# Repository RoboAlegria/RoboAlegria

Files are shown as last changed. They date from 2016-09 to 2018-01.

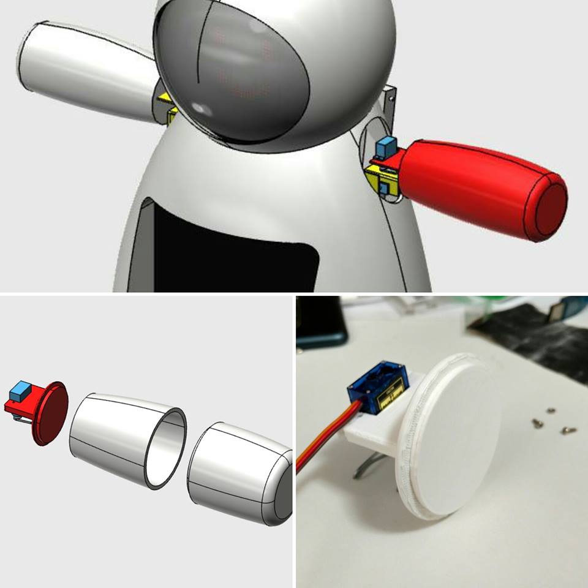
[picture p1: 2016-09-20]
modelo 3D/carenagem/images/impressão 3D-2.jpg

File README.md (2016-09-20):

# Robo da Alegria
Projeto de código aberto, com o objetivo de compartilhar conhecimentos sobre eletrônica, robótica e programação de computadores.

O objetivo geral do projeto é criar um Robô para ser utilizado no trabalho de ONGs como o Doutores da Alegria.

A estrutra dos diretórios está organizada para

appInventor: código do AppInventor para testar a comunicação via bluetooth com o Robô.
arduino: código do Arduino para o controle da expressão facial (matriz de leds)
images: imagens utilizadas no projeto
webservice: código da parte web para a interface que o operador controlar o robô
Mais informações na wiki do projeto: https://github.com/RoboAlegria/RoboAlegria/wiki

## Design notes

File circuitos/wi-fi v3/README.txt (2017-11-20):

Especificação:
- Acionamento de até 6 servo motores (J1, J2, J3, J4, J5 e J6)
- Acionamento de array de matrizes de LED
- Comunicação através de wi-fi (ESP8266)
- Alimentação dos servo motores por bateria externa

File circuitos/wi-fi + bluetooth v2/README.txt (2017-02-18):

Especificação do Shield:
- Shield para Arduino Uno
- Acionamento de até 5 servo motores (J1, J2, J3, J4 e J5)
- Acionamento de array de matrizes de LED (J6)
- Comuinicação através de bluetooth (HC-05 ou HC-06) (J7)
- Comunicação através de wi-fi (ESP8266) (J8)
- Alimentação do Arduino através de bateria externa (J15) - Colocar jumper em J12 para alimentação externa. Sem o jumper a alimentação será através da porta USB
- Alimentação dos servo motores por bateria externa (colocando jumper em J13 na posição +6V) ou diretamente do regulador de 5V do Arduino (colocando jumper em J13 na posição +5V)
- Acionamento de até quatro motores DC (J9 e J10)
- Remover jumper do conector J11 para programação
- Barramento para alimentação externa +5V de outros periféricos (J16 e J17)
- Pinos para entradas/saídas analógicas/digitais adicionais (J18)

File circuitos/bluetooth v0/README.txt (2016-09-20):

Especificação do Shield:
- Shield para Arduino Uno
- Acionamento de até 2 servo motores
- Acionamento de array de matrizes de LED
- Comuinicação através de bluetooth (HC-05 ou HC-06)

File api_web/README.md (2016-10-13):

# Robô da Alegria  

## API para desenvolvimento, simulando as ações do robô.  
  
O objeto deste API é simular as ações do robô para os desenvolvedores de aplicativos usarem os mesmo comandos que serão recebidos pelo robô.  

### Descrição:  
A URL inicial (/) mostra em uma página html a lista de comandos válidos;  
A URL /command-list mostra em formato JSON a lista de comandos válidos;  
A URL /?{PARAMETRO}={COMANDO} mostra o comando enviado;  

API dispinivel online pelo endereço: http://robodaalegria.hmxweb.com/

API desenvolvida com PHP, utilzando o microframework Slim.

http://www.slimframework.com

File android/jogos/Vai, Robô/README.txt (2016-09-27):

Por: Igor Fonseca Albuquerque
Baseado no jogo Droid-Run-Jump por Donald E. Llopis 2011 (https://github.com/machinezilla/DroidRunJump)

Um jogo de corrida para Android.

Desenolvido usando o Android 21.0 SDK.

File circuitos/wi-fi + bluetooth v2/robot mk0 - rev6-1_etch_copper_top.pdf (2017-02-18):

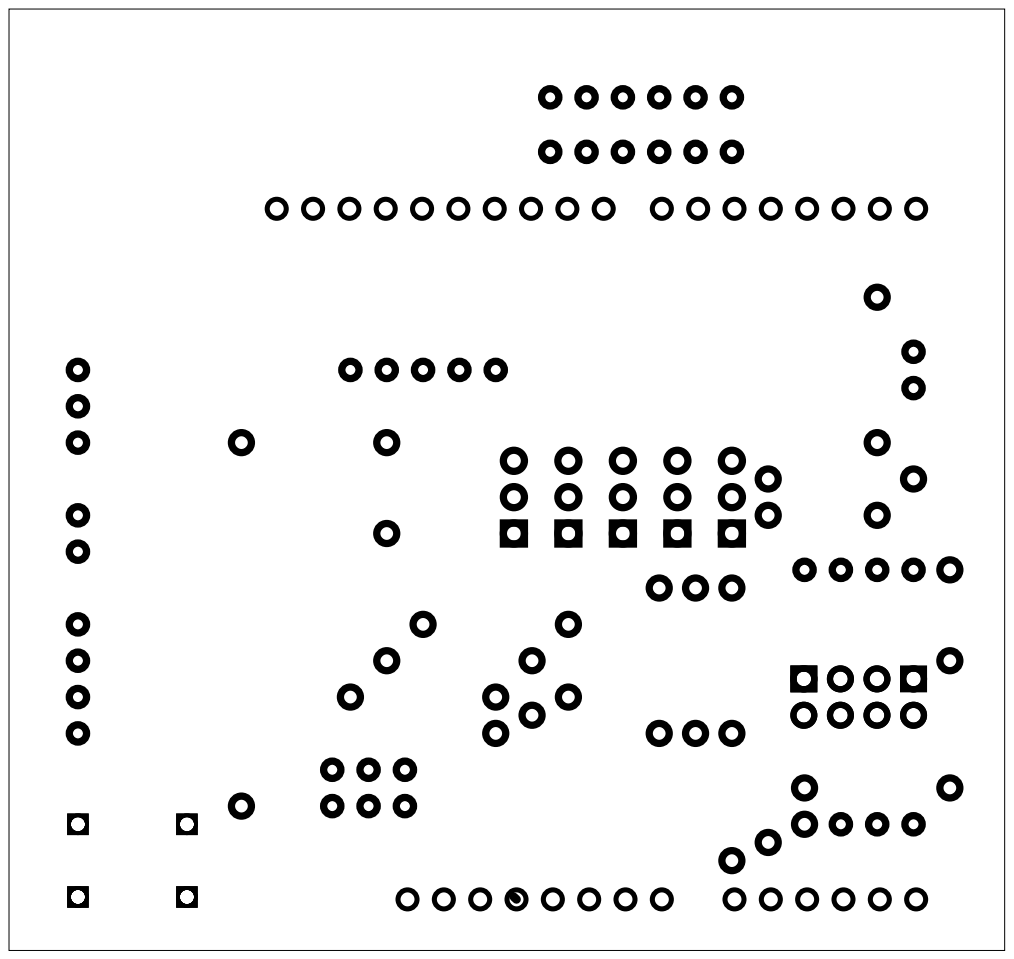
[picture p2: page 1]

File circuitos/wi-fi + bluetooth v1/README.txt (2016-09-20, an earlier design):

Especificação do Shield:
- Shield para Arduino Uno
- Acionamento de até 4 servo motores (J2, J3, J9 e J10)
- Acionamento de array de matrizes de LED (J8)
- Comuinicação através de bluetooth (HC-05 ou HC-06) (J7)
- Comunicação através de wi-fi (ESP8266) (U3)
- Alimentação dos servo motores por bateria externa (via USB em U2) ou diretamente do regulador de 5V do Arduino (seleção pelo jumper J13)

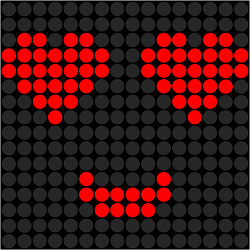
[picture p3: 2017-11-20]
interface html/full/images/rosto11.png

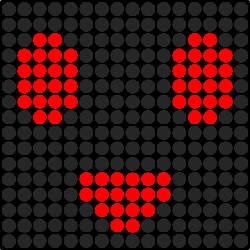
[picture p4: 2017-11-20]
interface html/full/images/rosto2.png

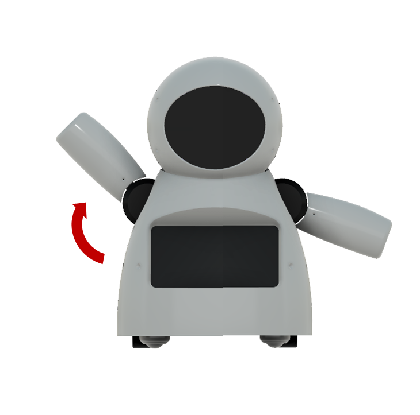
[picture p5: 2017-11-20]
interface html/full/images/mov02.png

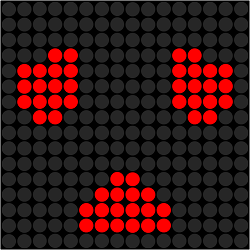
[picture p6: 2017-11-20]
interface html/full/images/rosto4.png

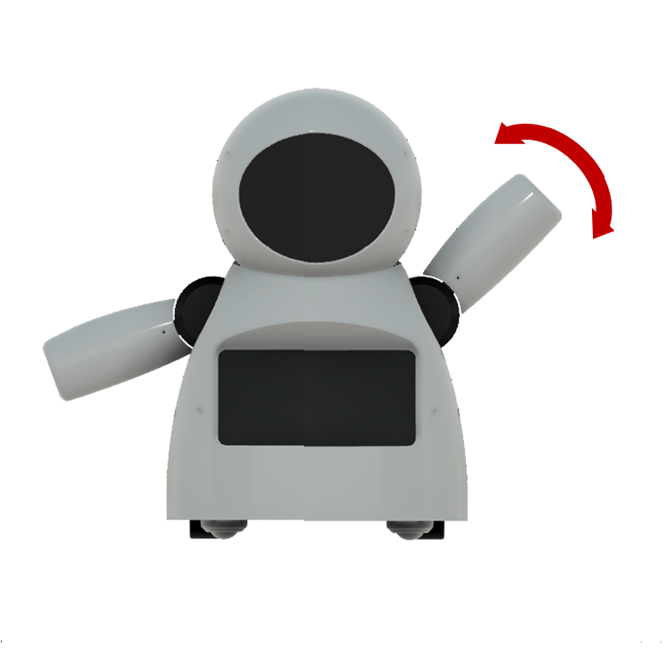
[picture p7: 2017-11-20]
interface html/full/images/mov09.png

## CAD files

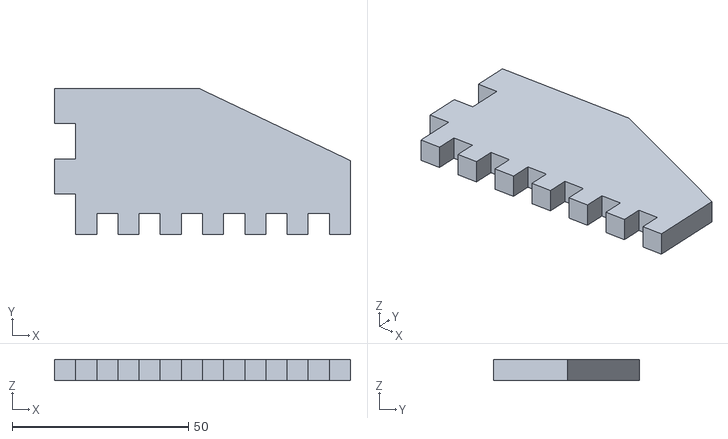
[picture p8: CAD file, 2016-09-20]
modelo 2D/p9.stl
84.0 x 41.5 x 6.00

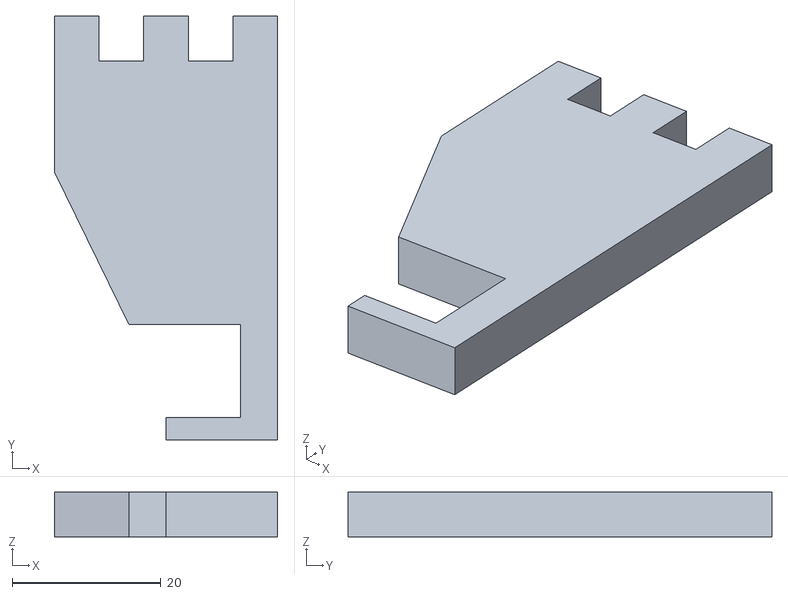
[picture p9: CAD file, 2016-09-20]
modelo 2D/p8.stl
30.0 x 57.0 x 6.00

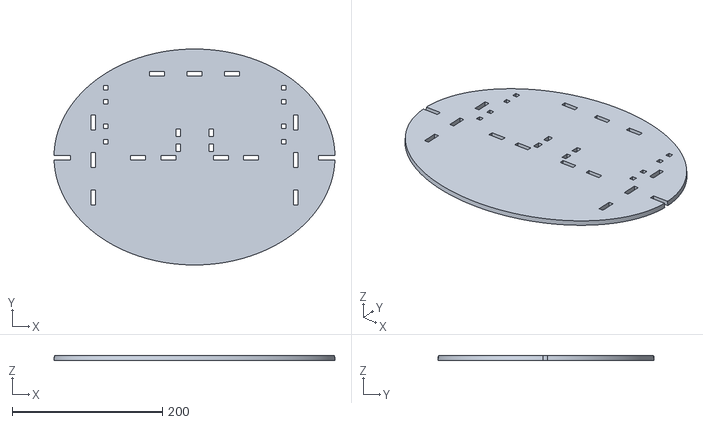
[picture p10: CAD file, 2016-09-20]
modelo 2D/p2.stl
374.3 x 287.6 x 6.00

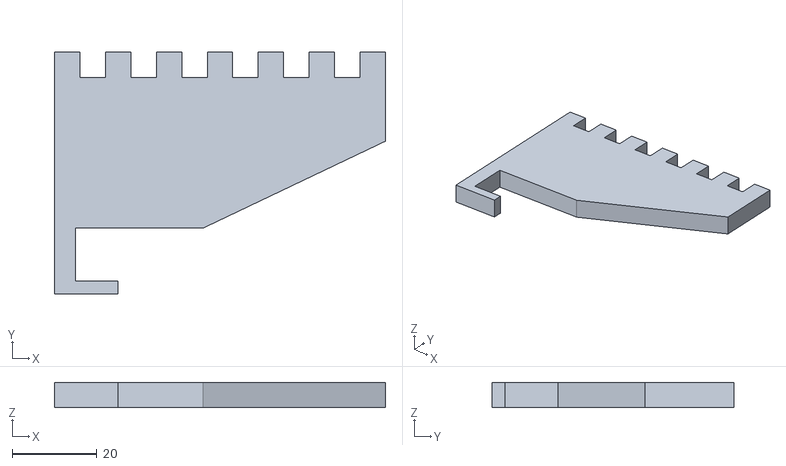
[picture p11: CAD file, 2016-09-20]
modelo 2D/p7.stl
78.0 x 57.0 x 6.00

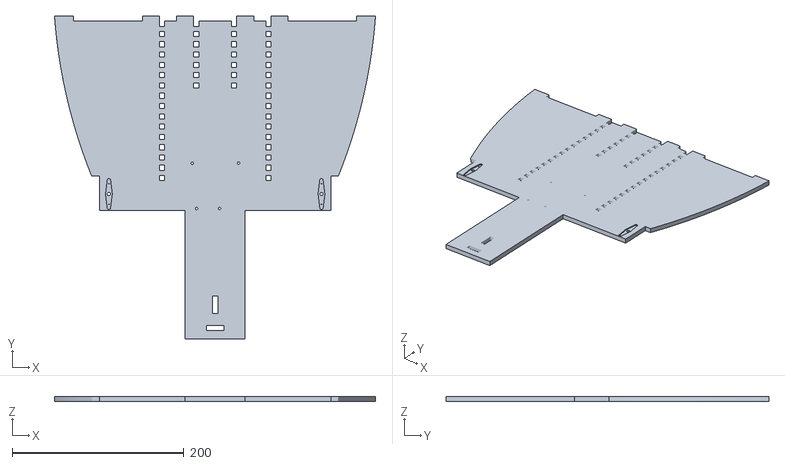
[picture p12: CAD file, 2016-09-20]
modelo 2D/p6.stl
374.3 x 376.6 x 6.00

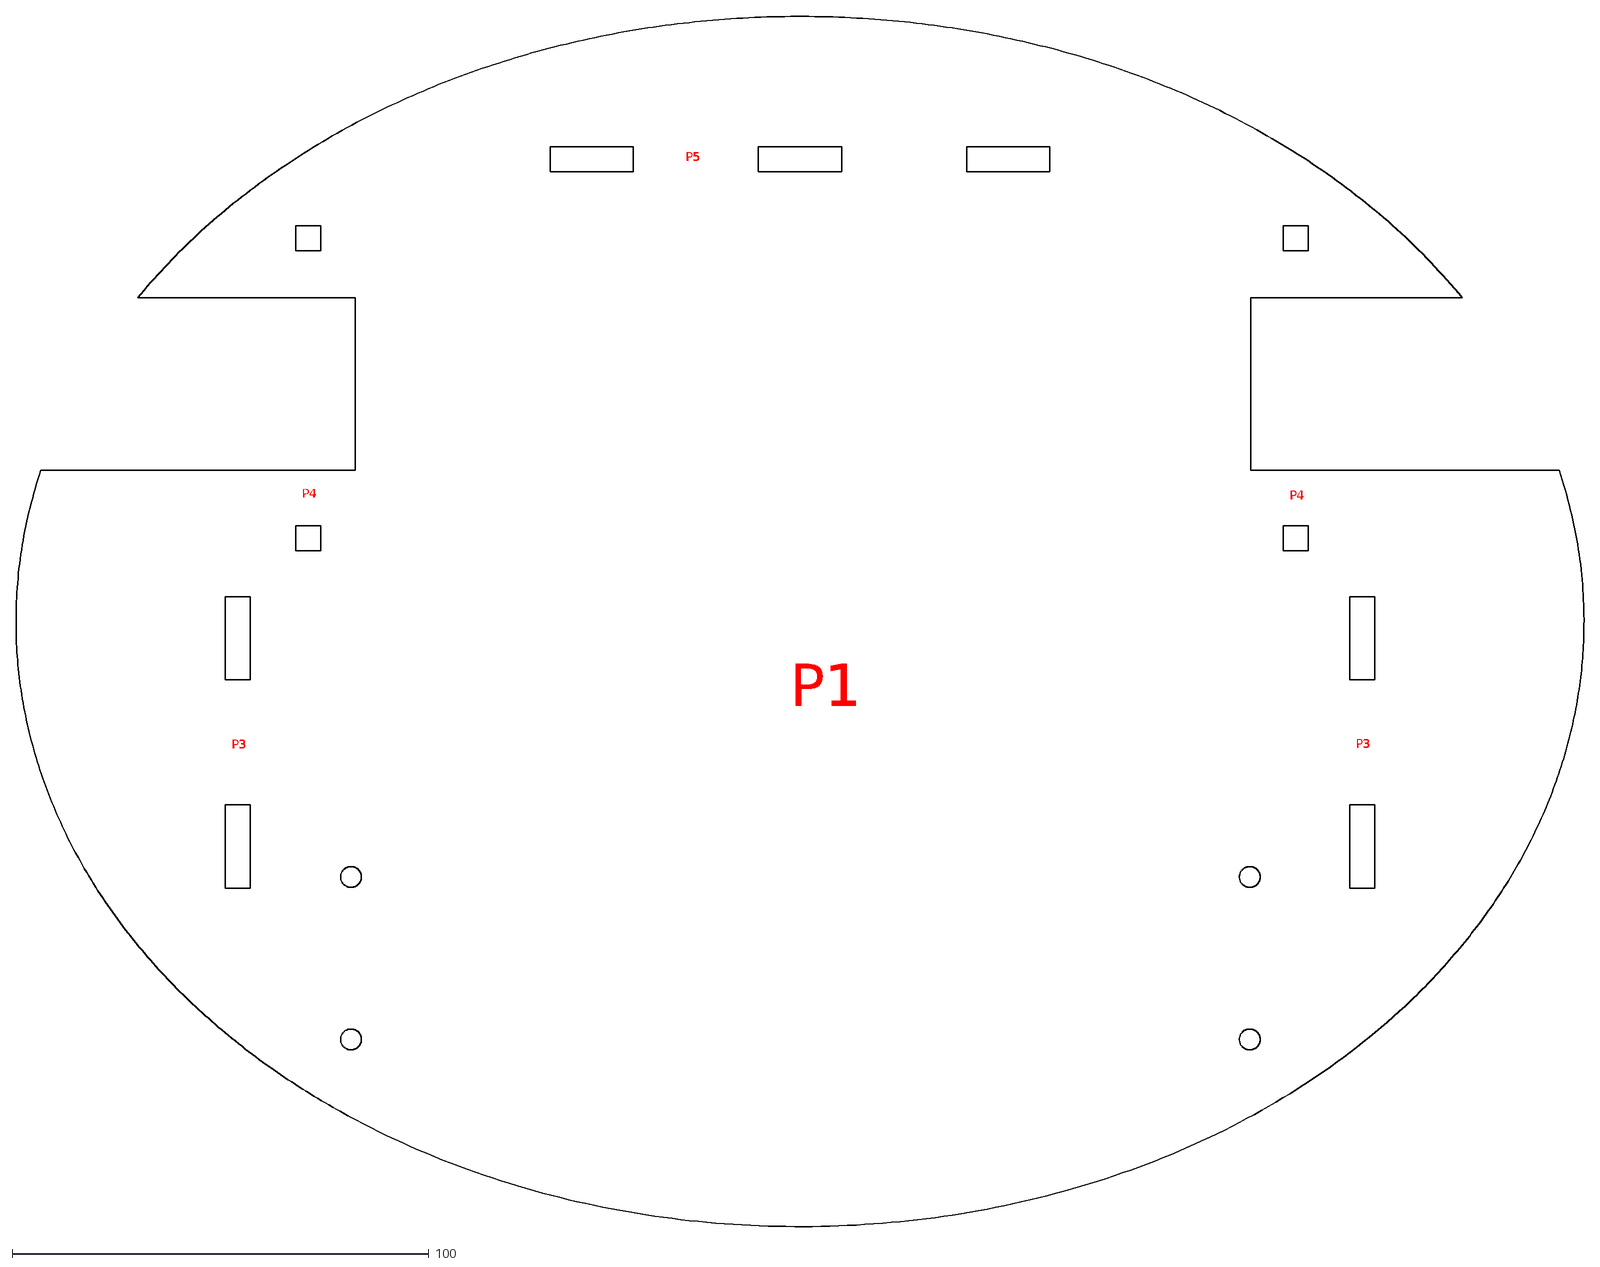
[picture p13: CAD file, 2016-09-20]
modelo 2D/p1.dxf
P1
P3
P4
P5

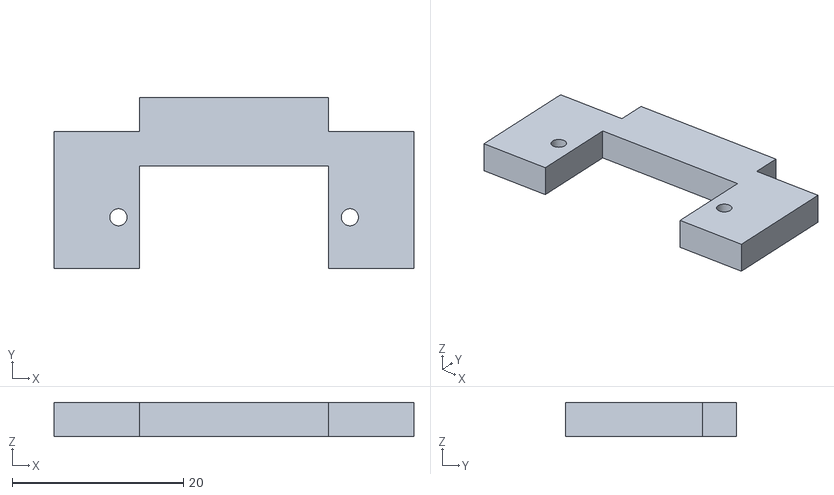
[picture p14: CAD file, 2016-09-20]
modelo 2D/p13.stl
42.0 x 20.0 x 4.00

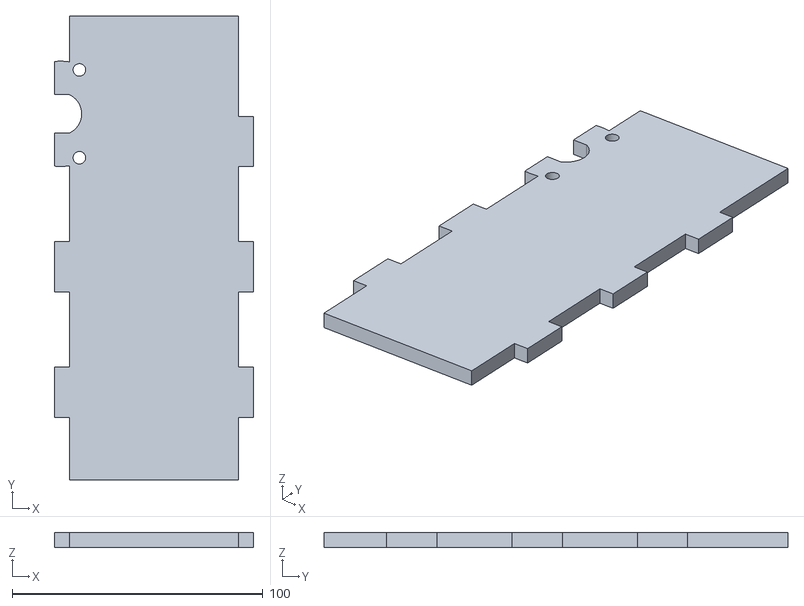
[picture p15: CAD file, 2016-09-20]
modelo 2D/p3.stl
79.5 x 185.0 x 6.00

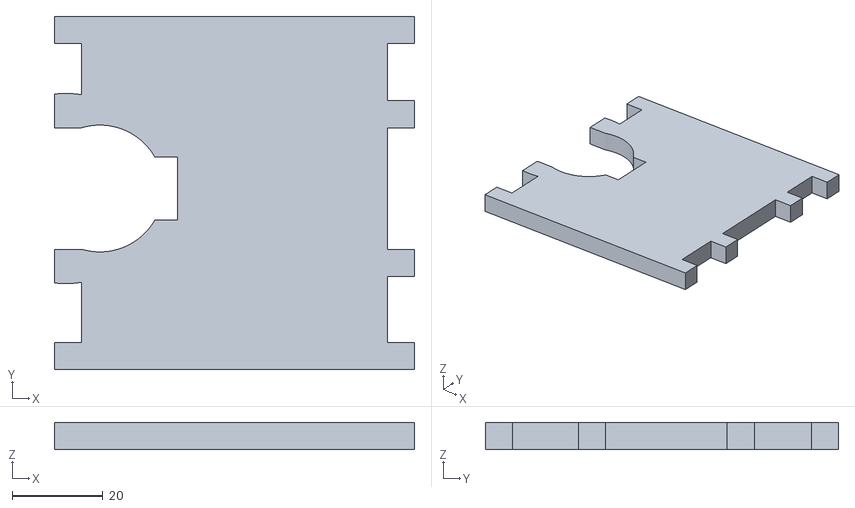
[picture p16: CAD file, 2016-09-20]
modelo 2D/p4.stl
79.5 x 78.0 x 6.00

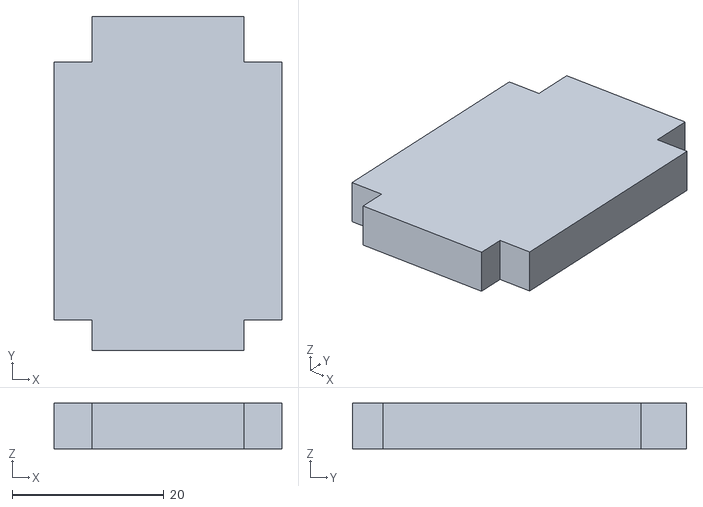
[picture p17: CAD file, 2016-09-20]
modelo 2D/p12.stl
30.0 x 44.0 x 6.00

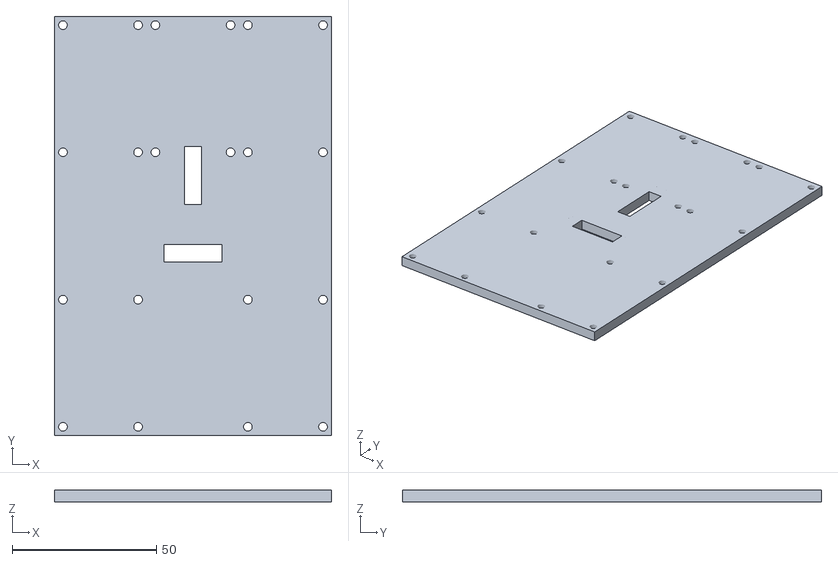
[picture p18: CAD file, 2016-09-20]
modelo 2D/p10.stl
96.0 x 145.0 x 4.00

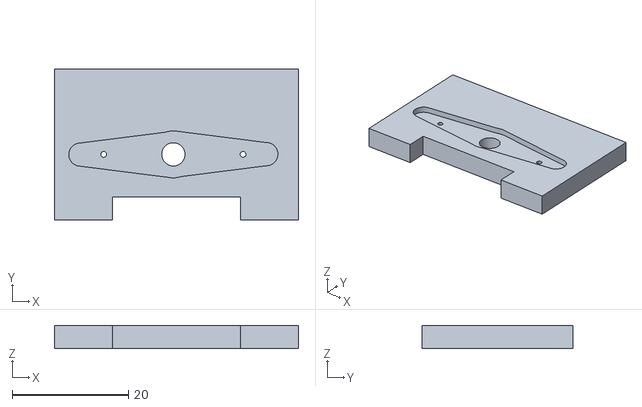
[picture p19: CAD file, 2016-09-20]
modelo 2D/p14.stl
42.0 x 26.0 x 4.00

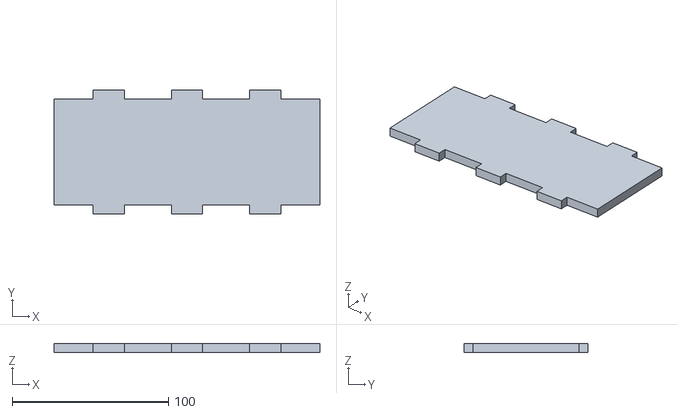
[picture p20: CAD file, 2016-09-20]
modelo 2D/p5.stl
170.0 x 79.5 x 6.00

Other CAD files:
modelo 2D/p11.stl
modelo 2D/p10.dwg
modelo 2D/p10.dxf
modelo 2D/p11.dxf
modelo 2D/p12.dxf
modelo 2D/p13.dxf
modelo 2D/p14.dxf
modelo 2D/p2.dxf
modelo 2D/p3.dxf
modelo 2D/p4.dxf
modelo 2D/p5.dxf
modelo 2D/p6.dxf
modelo 2D/p7.dxf
modelo 2D/p8.dxf
modelo 2D/p9.dxf

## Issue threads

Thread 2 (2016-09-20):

Bluetooh e Wifi como opcionais

ferauche, 2016-09-20:
Realizar alteraçoes de hardware (no shield) e no código, para deixar a conexão configurável, como uma opção para o usuário utilizar a conexão bluetooth ou wifi.

ferauche, 2016-09-20:
Aproveitar o novo desenho do shield para receber também os dois motores de passo responsáveis pela movimentação do robô.

igorfonseca83, 2017-02-18:
Motores adicionados ao shield. Adicionado conector para módulo bluetooth.

Closed 2017-02-18.

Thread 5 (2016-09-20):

Roteador dentro do robô

ferauche, 2016-09-20:
Pensar em solução de roteamento (Android + Arduino + Notebook/Smartphone) sendo realizado pelo próprio robô,

ferauche, 2017-07-25:
Criada uma VM Debian customizada para utilizar um adaptador USB WiFI como roteador plugada diretamente no Notebook. VM ficou com 2,7 GB.

As informações de como montar a VM estão em: http://ferauche.blogspot.com.br/2017/03/vm-linux-para-servir-como-access-point.html

Closed 2017-07-25.

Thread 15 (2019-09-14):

LED pins not correct

rolandschuetz, 2019-09-14:
Hello,

[the code](https://github.com/RoboAlegria/RoboAlegria/blob/master/arduino/RoboAlegria/RoboAlegria.ino#L23) expects the pins like this
Pinos 9 (DIN), 10 (CLK), 11 (CS)

But the [hardware schema] (https://cdn.instructables.com/FOY/GJDK/JCKUNMKH/FOYGJDKJCKUNMKH.LARGE.jpg) connects CLK to PIN 11

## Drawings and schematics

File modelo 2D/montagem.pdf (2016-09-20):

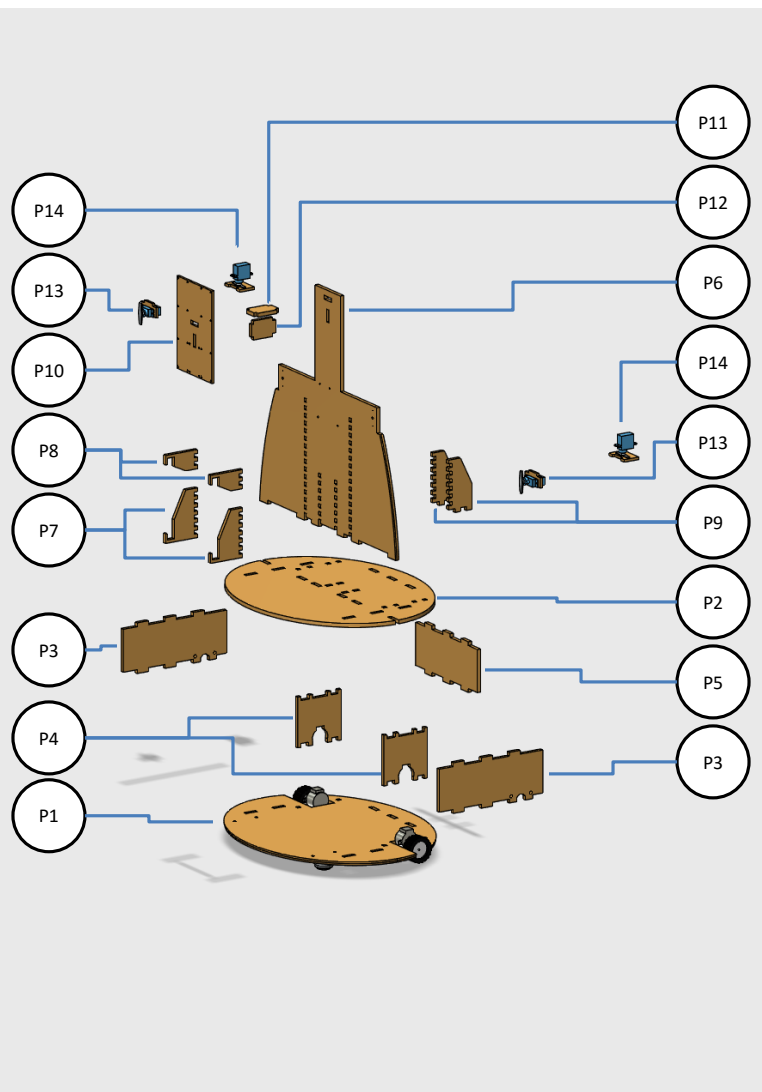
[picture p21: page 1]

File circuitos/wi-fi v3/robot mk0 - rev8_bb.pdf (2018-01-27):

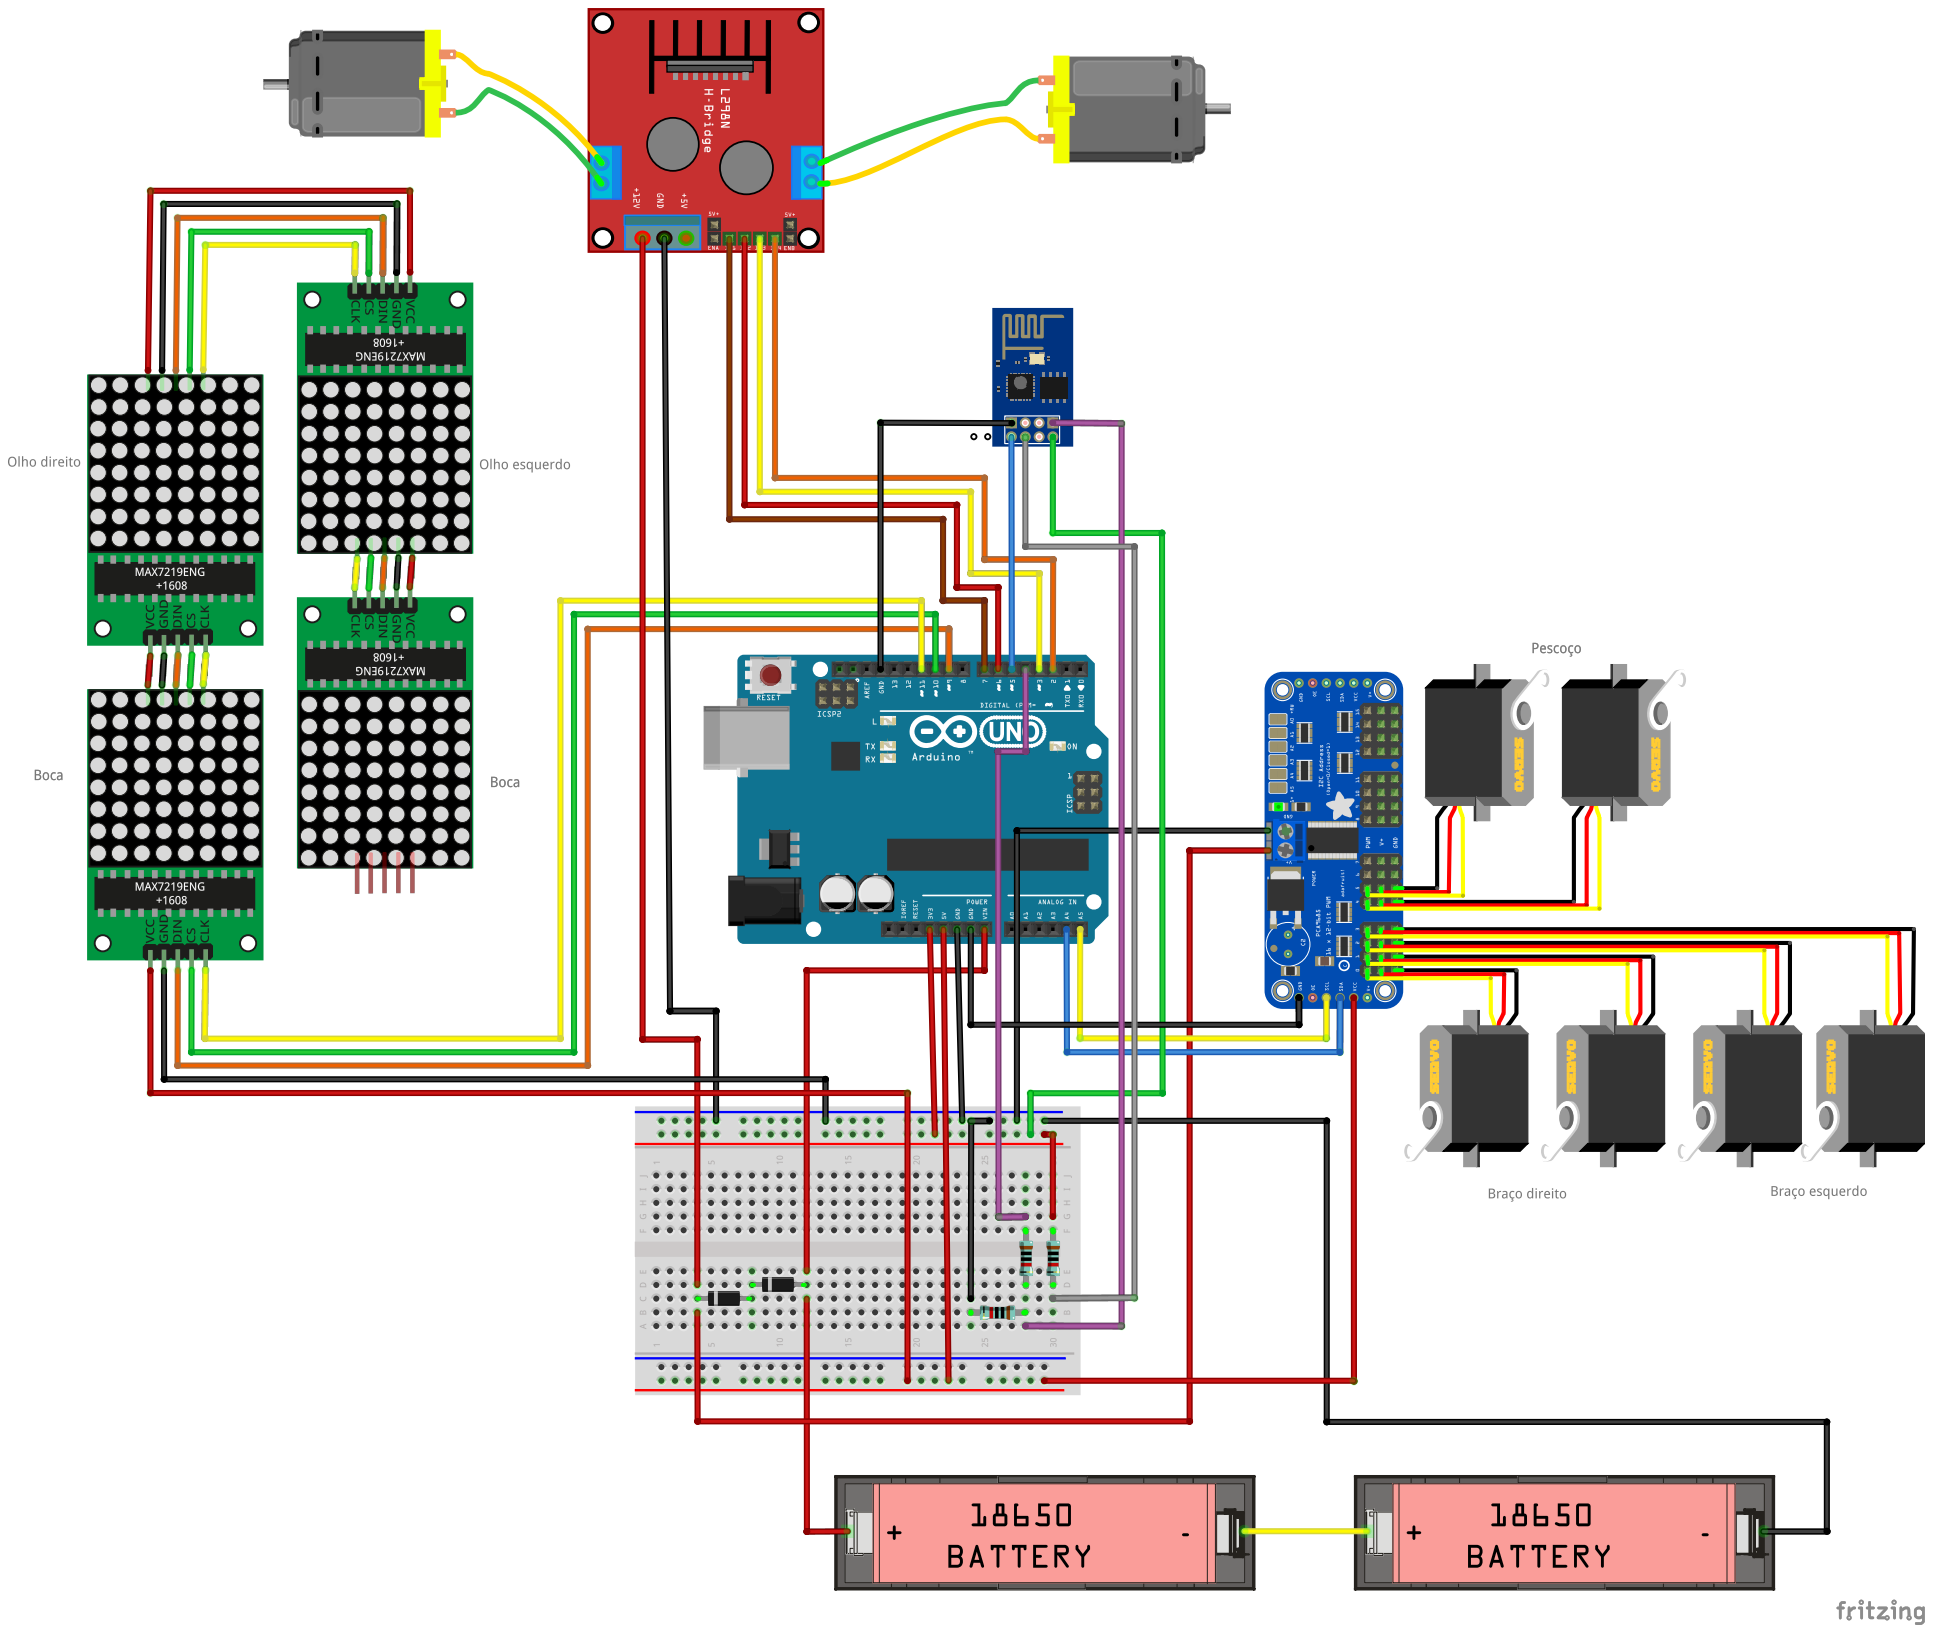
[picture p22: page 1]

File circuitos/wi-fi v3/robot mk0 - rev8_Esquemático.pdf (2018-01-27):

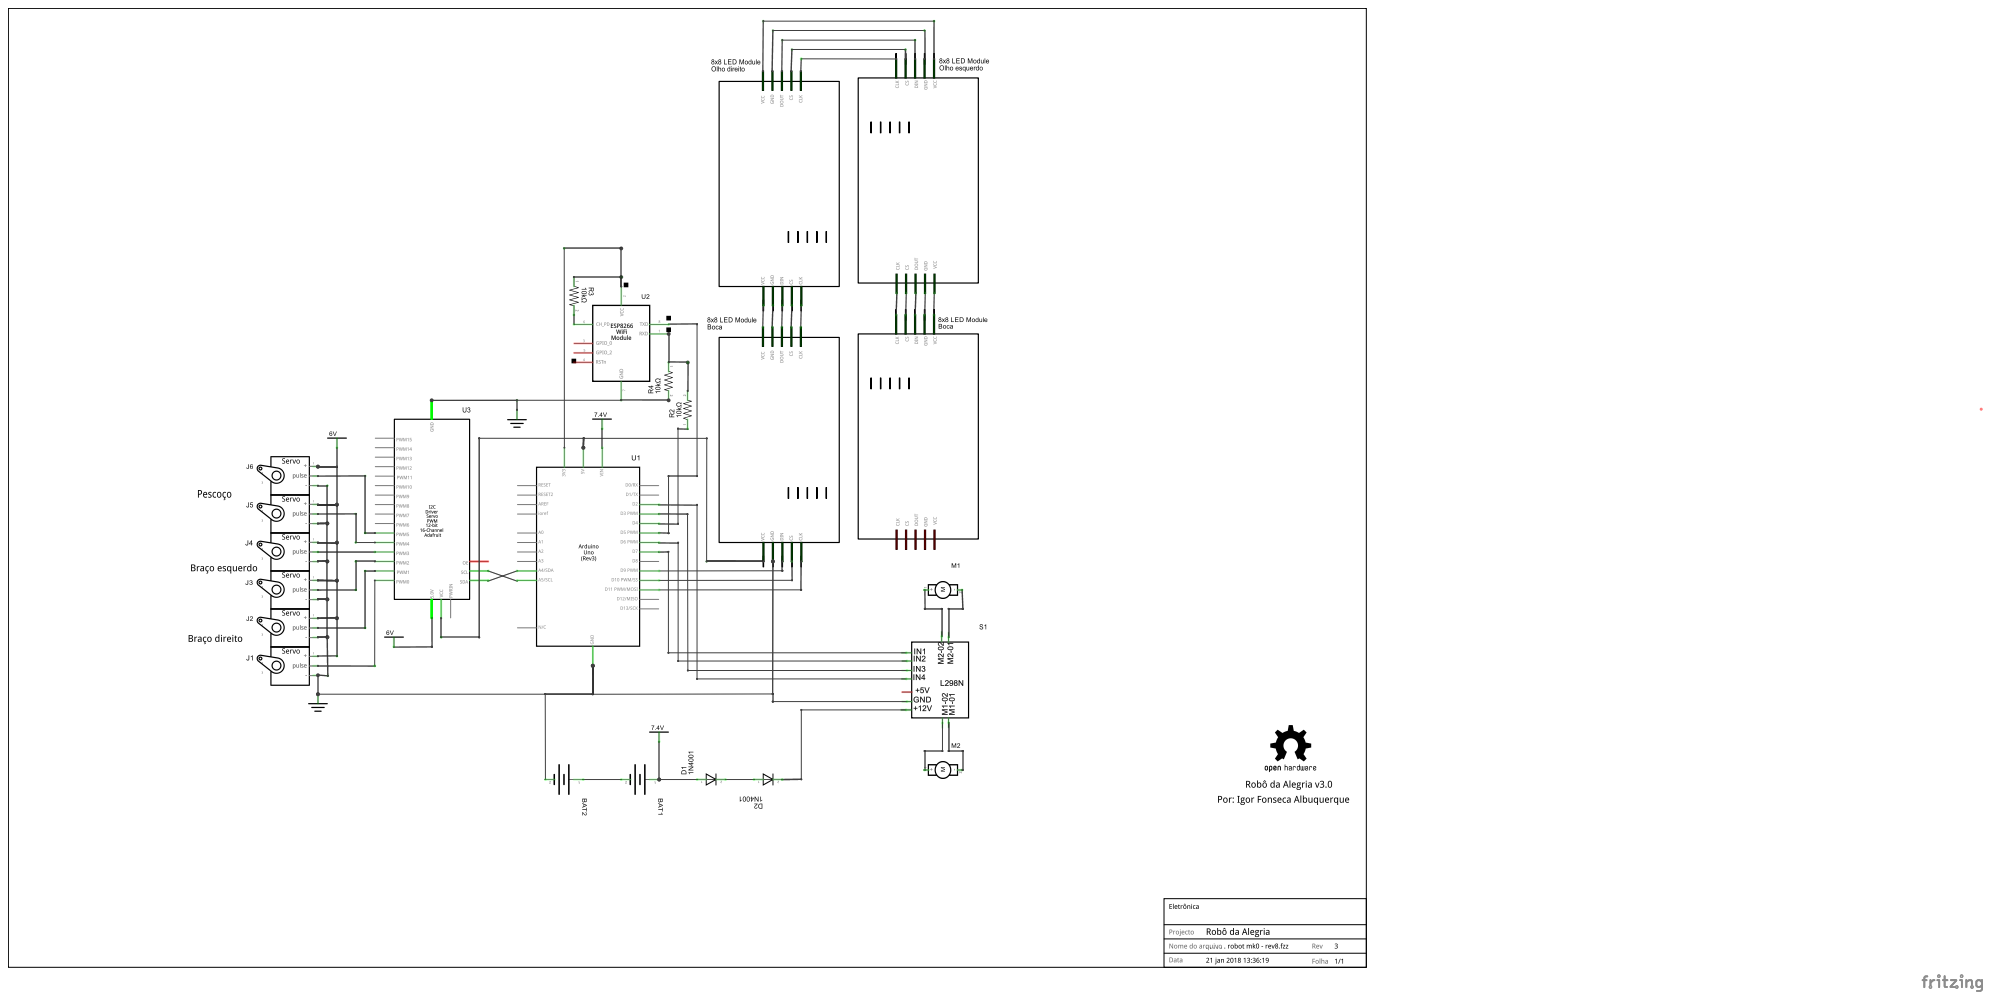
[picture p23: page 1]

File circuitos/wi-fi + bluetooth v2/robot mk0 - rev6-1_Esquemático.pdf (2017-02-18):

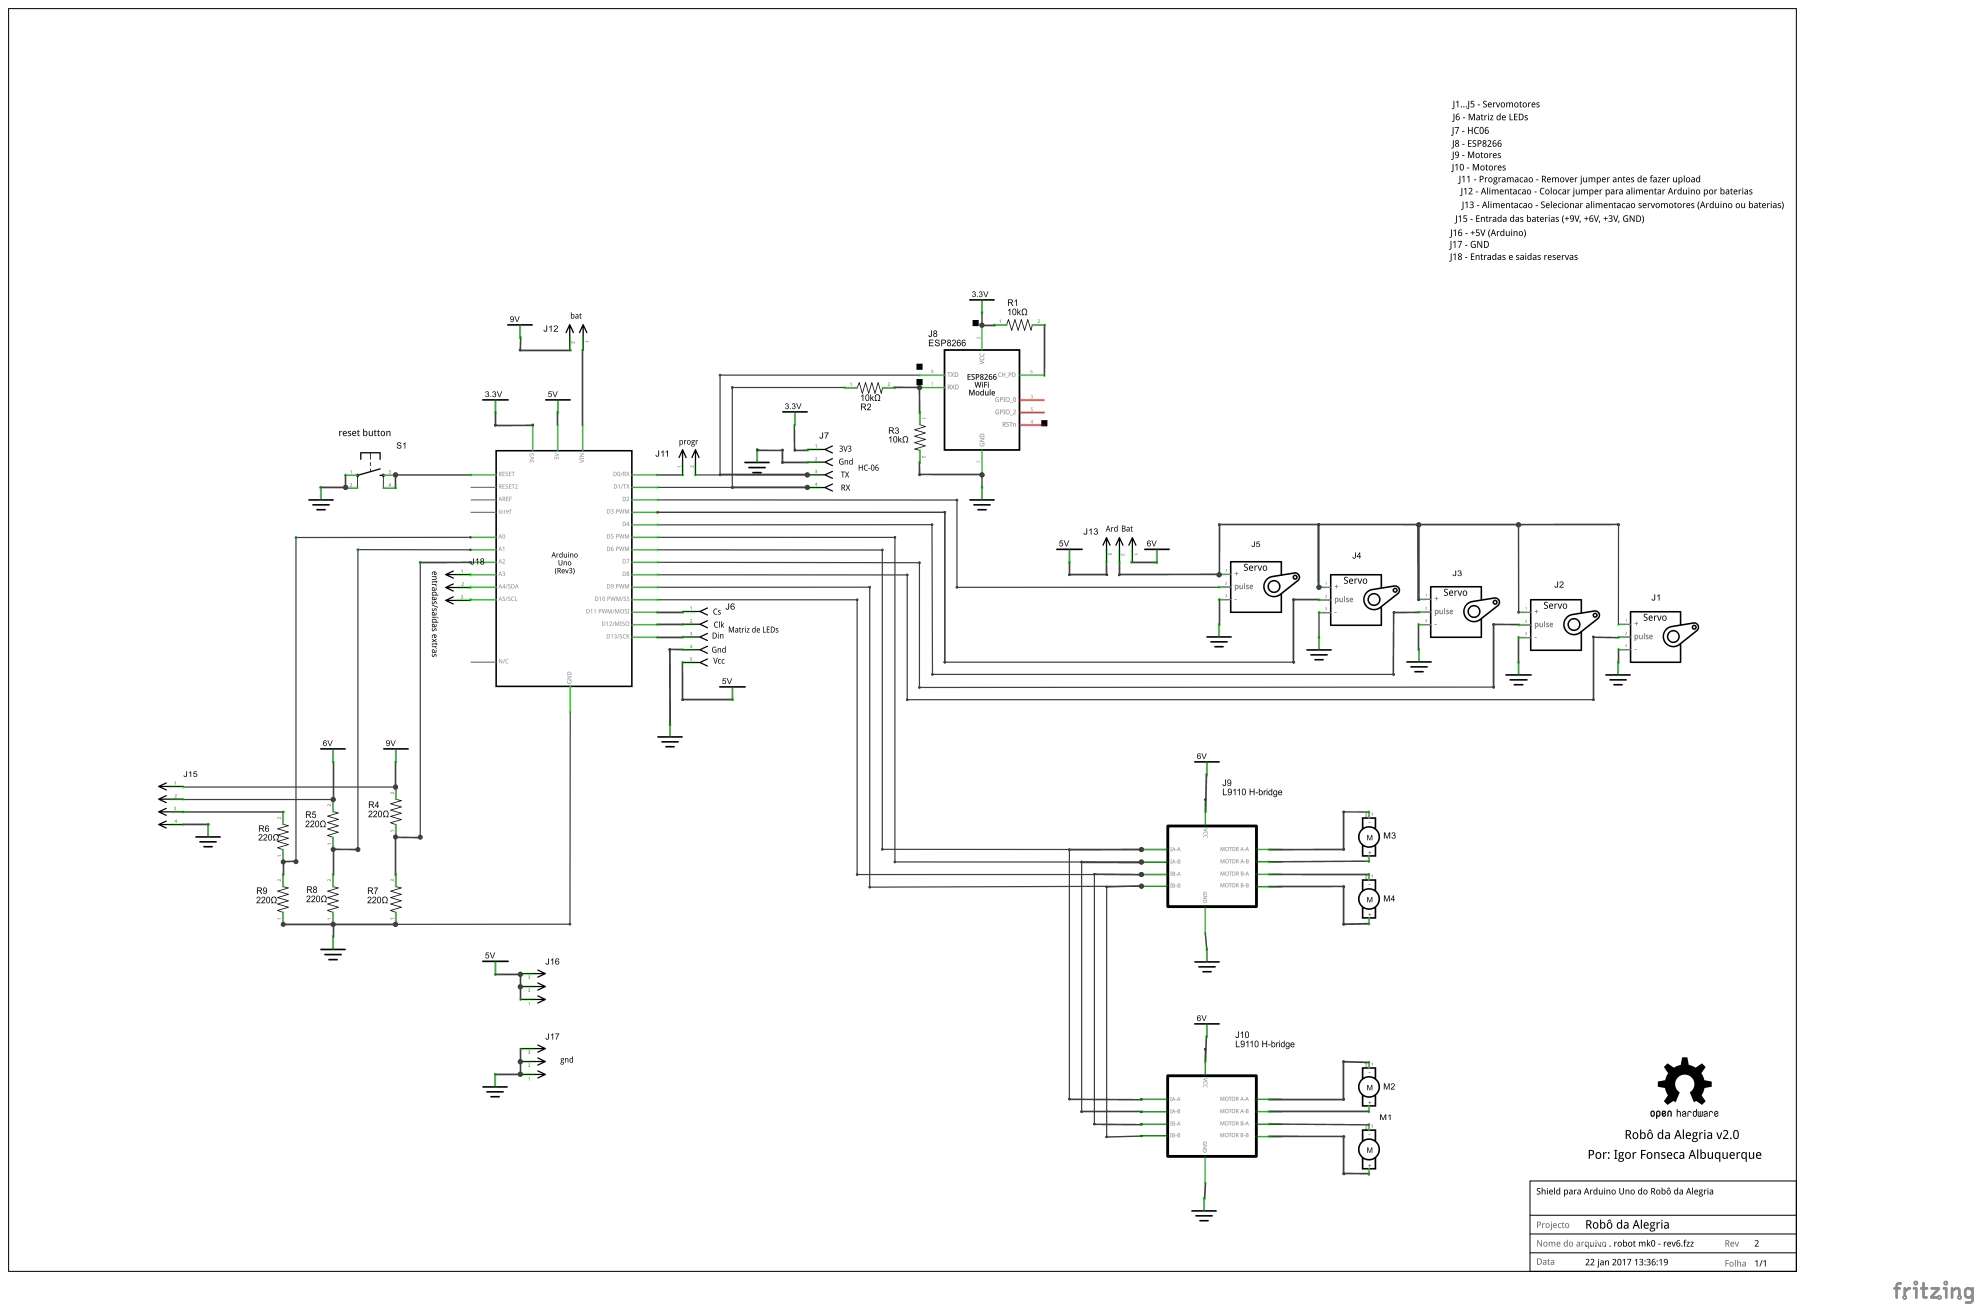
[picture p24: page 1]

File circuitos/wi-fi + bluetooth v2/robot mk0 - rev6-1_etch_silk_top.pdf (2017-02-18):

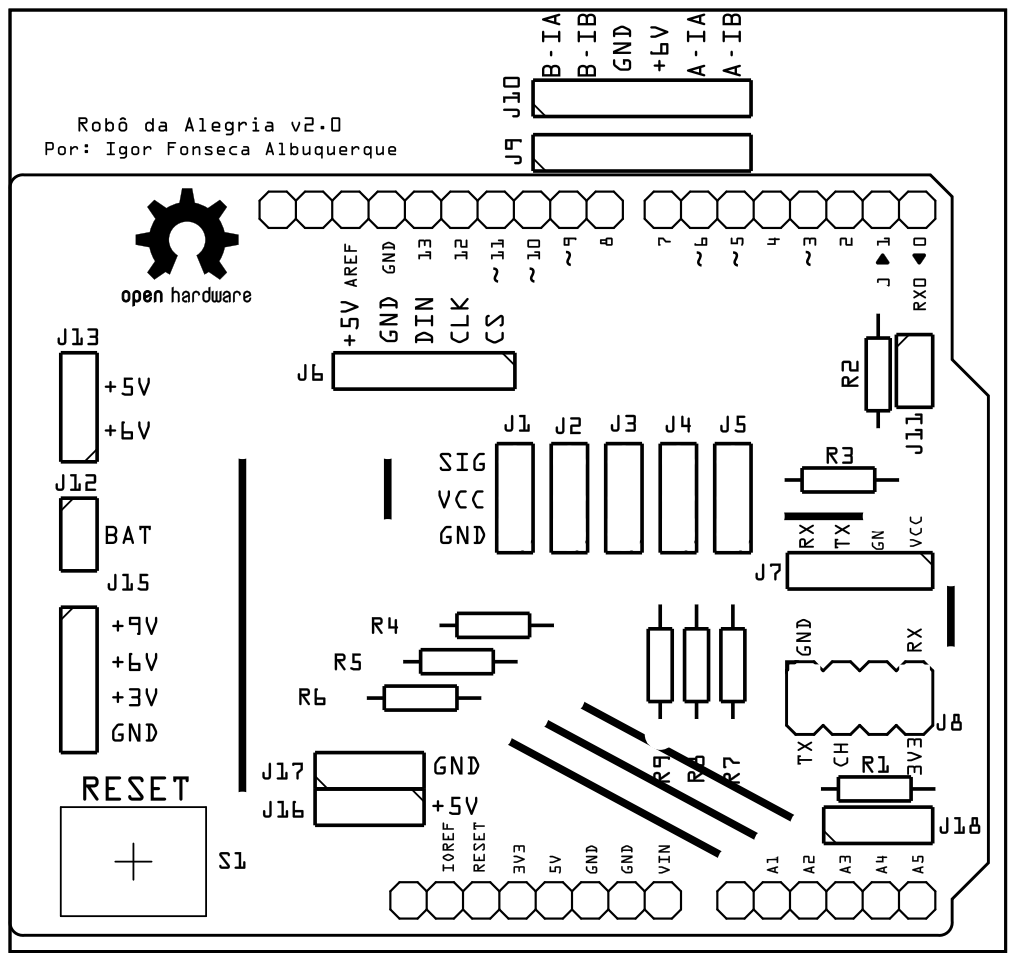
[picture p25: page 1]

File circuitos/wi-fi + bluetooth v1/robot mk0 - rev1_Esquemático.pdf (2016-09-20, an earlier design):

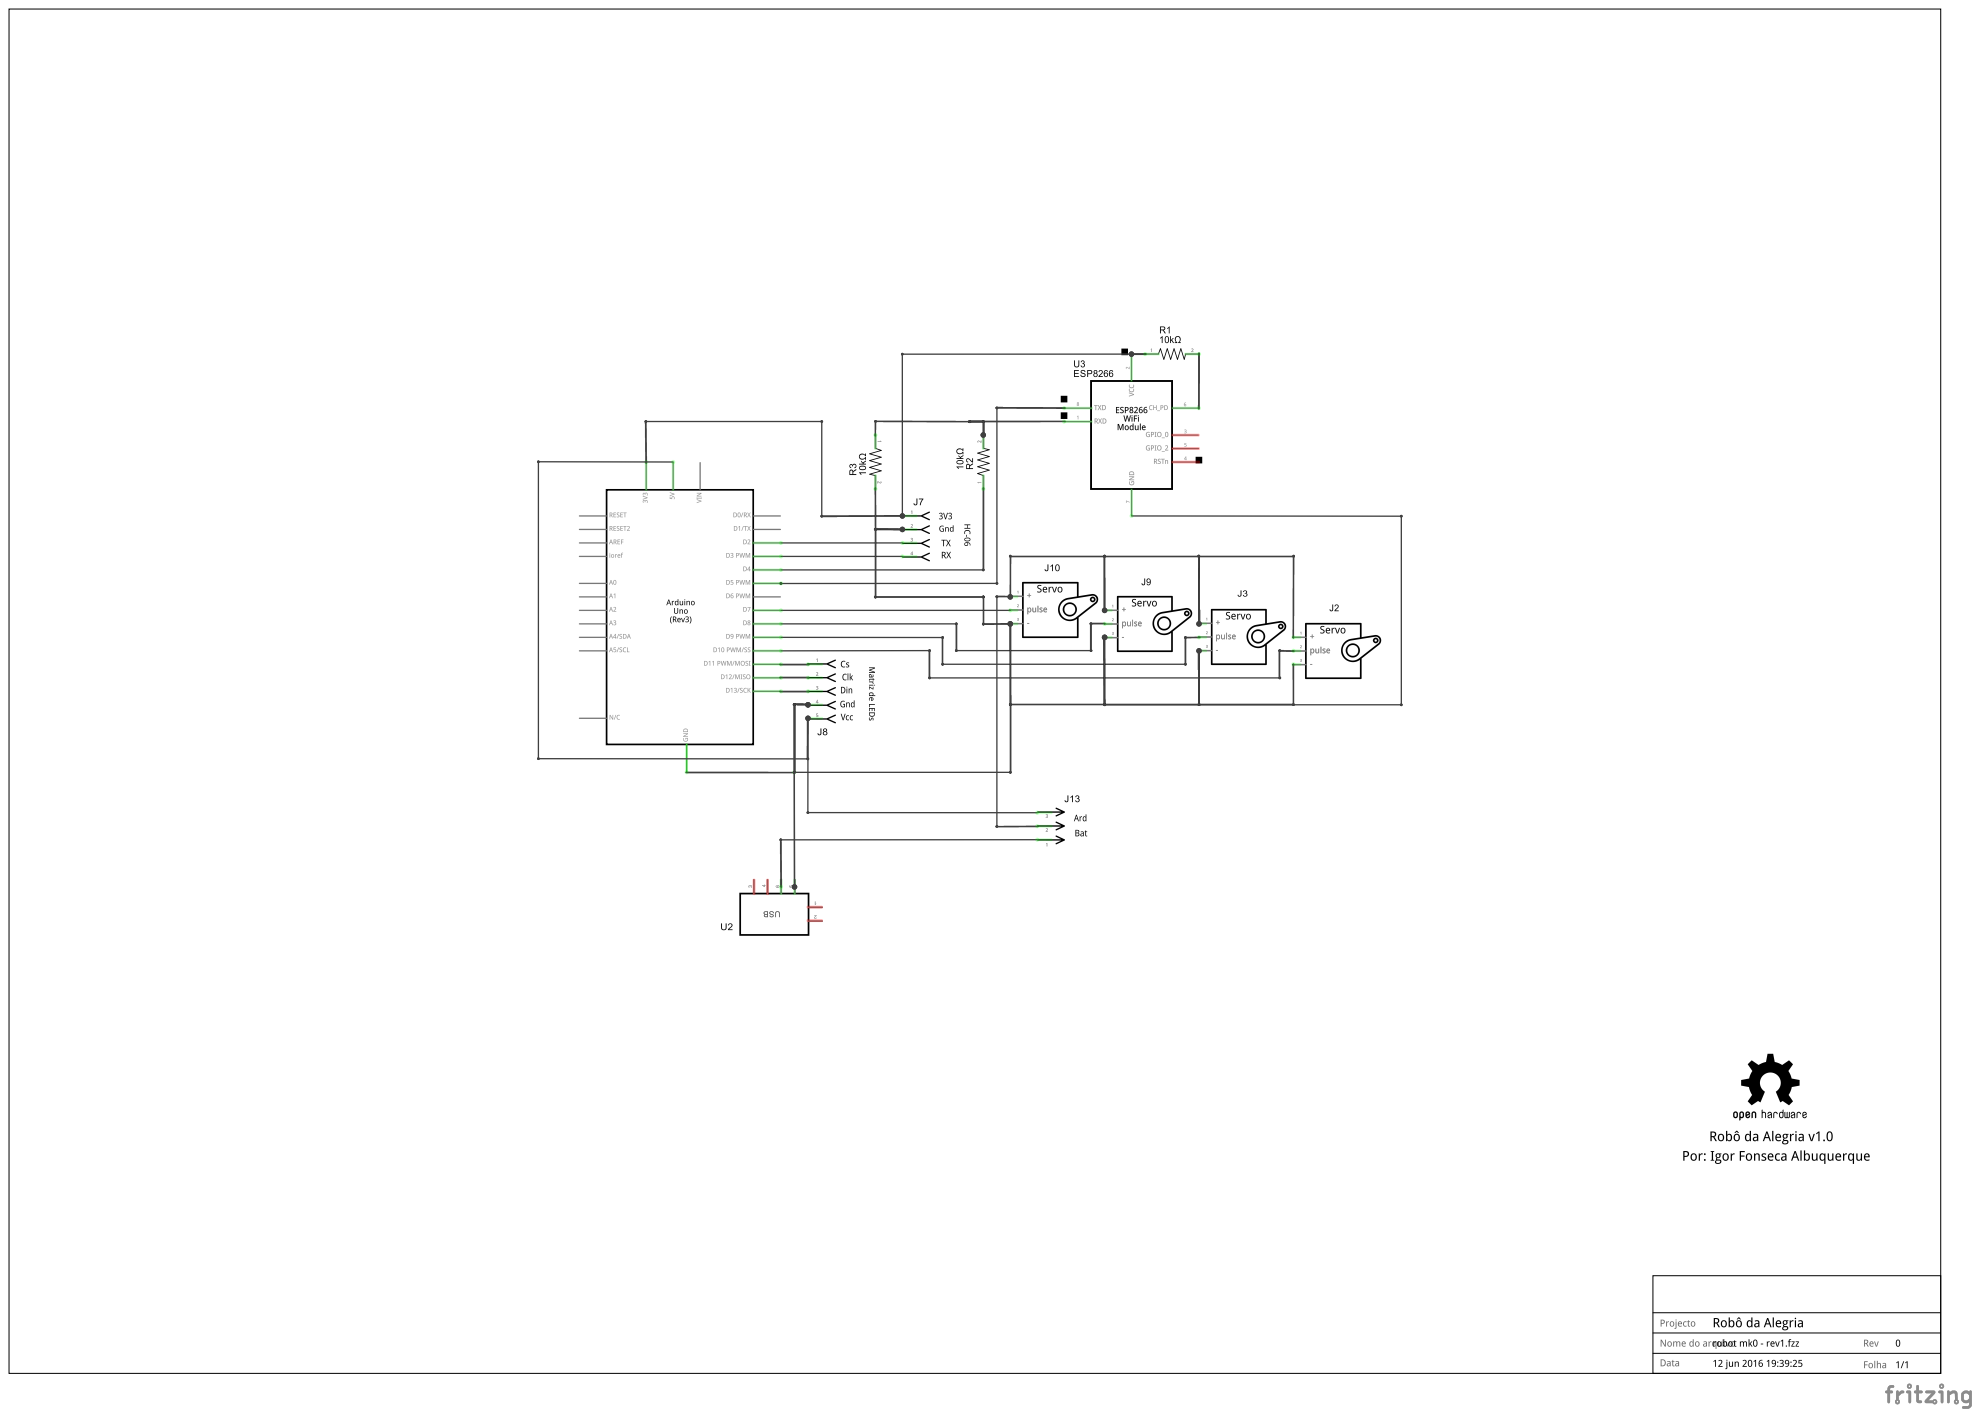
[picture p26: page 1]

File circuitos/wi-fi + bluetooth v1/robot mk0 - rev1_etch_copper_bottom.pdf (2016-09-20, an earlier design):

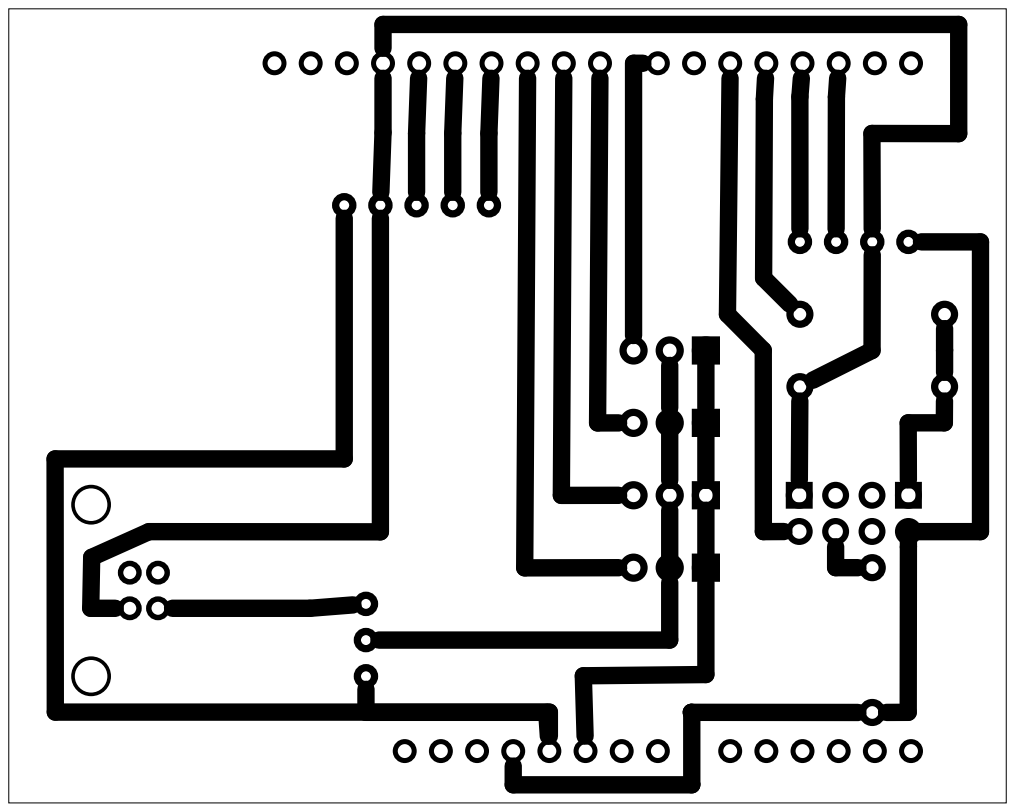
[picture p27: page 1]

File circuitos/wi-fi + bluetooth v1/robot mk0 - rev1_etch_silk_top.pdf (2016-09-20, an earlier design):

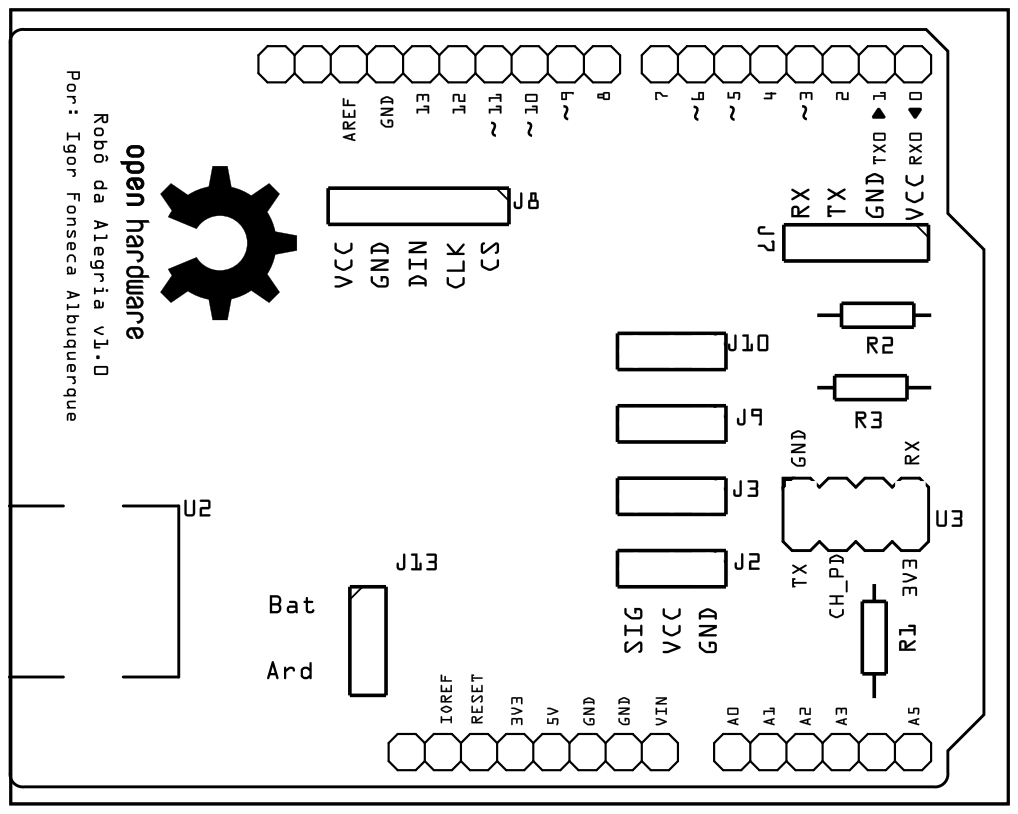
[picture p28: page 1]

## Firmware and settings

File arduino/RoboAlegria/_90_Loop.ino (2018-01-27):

//*************************
//Loop principal do Arduino
//*************************
void loop()
{
  int delta = millis() - tempo0;
  if(delta > 3000) {              //se o tempo for superior a 10 segundos
    if(piscar == true) {
//    display_olhos(olho_dormindo, olho_dormindo);  //piscar olhos
      display_olhos(olho_fechado_baixo_e, 2);  //piscar olhos
      display_olhos(olho_fechado_baixo_d, 1);  //piscar olhos
      delay(200);
      restore();
      tempo0 = millis();
    }
  }
  
  if (esp8266.available())  //verifica se o ESP8266 está recebendo dados
  {
    if (esp8266.find("+IPD,")) //se tiver recebido um dado
    {
      String msg;
      esp8266.find("?"); //corre o cursor até encontrar o comando na mensagem recebida     
      msg = esp8266.readStringUntil(' '); //ler string até o fim da mensagem
      String comando = msg.substring(0, 3); //primeiros 3 caracteres da mensagem = comando
      String valorStr = msg.substring(4);   //3 caracteres seguintes = valor associado ao comando
      int valor = valorStr.toInt();         //conversão de valor para inteiro
      if (DEBUG) {
        Serial.println(comando);
        Serial.println(valor);
      }
      delay(100);
      
      //*********************************************************
      //realizar ações: movimentar servos para ângulos informados
      //*********************************************************
      
      //mover o servo1 no angulo recebido em valor
      if(comando == "sr1") {
         //limitar o angulo de entrada
         if (valor >= pos1max) {
           valor = pos1max;
         }
         if (valor <= pos1min) {
           valor = pos1min;
         }
         //avançar até o ângulo desejado
         while(pos1 != valor) {
           if (pos1 > valor) {
             pos1 -= 1;
             pwm.setPWM(0, 0, map(pos1, 0, 180, SERVOMIN, SERVOMAX));
             delay(100/vel);
           }
           if (pos1 < valor) {
             pos1 += 1;
             pwm.setPWM(0, 0, map(pos1, 0, 180, SERVOMIN, SERVOMAX));
             delay(100/vel);
           }
         }
      }

      //mover o servo2 no angulo recebido em valor
      if(comando == "sr2") {
         //limitar o angulo de entrada
         if (valor >= pos2max) {
           valor = pos2max;
         }
         if (valor <= pos2min) {
           valor = pos2min;
         }
         while(pos2 != valor) {
           if (pos2 > valor) {
             pos2 -= 1;
             pwm.setPWM(1, 0, map(pos2, 0, 180, SERVOMIN, SERVOMAX));
             delay(100/vel);
           }
           if (pos2 < valor) {
             pos2 += 1;
             pwm.setPWM(1, 0, map(pos2, 0, 180, SERVOMIN, SERVOMAX));
             delay(100/vel);
           }
         }   
      }
      
      //mover o servo3 no angulo recebido em valor
      if(comando == "sr3") {
         //limitar o angulo de entrada
         valor = 180 - valor;
         if (valor >= pos3max) {
           valor = pos3max;
         }
         if (valor <= pos3min) {
           valor = pos3min;
         }
         while(pos3 != valor) {
           if (pos3 > valor) {
             pos3 -= 1;
             pwm.setPWM(2, 0, map(pos3, 0, 180, SERVOMIN, SERVOMAX));
             delay(100/vel);
           }
           if (pos3 < valor) {
             pos3 += 1;
             pwm.setPWM(2, 0, map(pos3, 0, 180, SERVOMIN, SERVOMAX));
             delay(100/vel);
           }
         }   
      }
      
      //mover o servo4 no angulo recebido em valor
      if(comando == "sr4") {
         valor = 180 - valor;
         //limitar o angulo de entrada
         if (valor >= pos4max) {
           valor = pos4max;
         }
         if (valor <= pos4min) {
           valor = pos4min;
         }        
         while(pos4 != valor) {
           if (pos4 > valor) {
             pos4 -= 1;
             pwm.setPWM(3, 0, map(pos4, 0, 180, SERVOMIN, SERVOMAX));
             delay(100/vel);
           }
           if (pos4 < valor) {
             pos4 += 1;
             pwm.setPWM(3, 0, map(pos4, 0, 180, SERVOMIN, SERVOMAX));
             delay(100/vel);
           }
         }       
      }

      //mover o servo5 no angulo recebido em valor
      if(comando == "sr5") {
         //limitar o angulo de entrada
         if (valor >= pos5max) {
           valor = pos5max;
         }
         if (valor <= pos5min) {
           valor = pos5min;
         }        
         while(pos5 != valor) {
           if (pos5 > valor) {
             pos5 -= 1;
             pwm.setPWM(4, 0, map(pos5, 0, 180, SERVOMIN, SERVOMAX));
             delay(100/vel);
           }
           if (pos5 < valor) {
             pos5 += 1;
             pwm.setPWM(4, 0, map(pos5, 0, 180, SERVOMIN, SERVOMAX));
             delay(100/vel);
           }
         }       
      }

      //mover o servo6 no angulo recebido em valor
      if(comando == "sr6") {
         valor = 180 - valor;
         //limitar o angulo de entrada
         if (valor >= pos6max) {
           valor = pos6max;
         }
         if (valor <= pos6min) {
           valor = pos6min;
         }        
         while(pos6 != valor) {
           if (pos6 > valor) {
             pos6 -= 1;
             pwm.setPWM(5, 0, map(pos6, 0, 180, SERVOMIN, SERVOMAX));
             delay(100/vel);
           }
           if (pos6 < valor) {
             pos6 += 1;
             pwm.setPWM(5, 0, map(pos6, 0, 180, SERVOMIN, SERVOMAX));
             delay(100/vel);
           }
         }       
      }


      //**************************************
      //realizar ações: movimentos programados
      //**************************************

      if(comando == "mov") {

        if(valor == 10) {
            mov1(); //movimento1 = levantar braço esquerdo
        }
        if(valor == 20) {
            mov2(); //movimento2 = levantar braço direito
        }
        if(valor == 30) {
            mov3(); //movimento3 = levantar os dois braços
        }
        if(valor == 40) {
            mov4(); //movimento4 = abaixar os dois braços
        }
        if(valor == 50) {
            mov5(); //movimento5 = balançar os dois braços abertos
        }
        if(valor == 60) {
            mov6(); //movimento6 = balançar os dois braços na frente
        }
        if(valor == 70) {
            mov7(); //movimento7 = balançar os dois braços na frente
        }
        if(valor == 80) {
            mov8(); //movimento8 = girar os braços
        }        
        if(valor == 90) {
            mov9(); //movimento 9 = aceno
        }

      }
      
      //**********************************
      //realizar ações: expressões da face
      //**********************************

      if(comando == "fac") {
        if(valor == 10) {
          fac1(); //feliz
        }
        if(valor == 20) {
          fac2(); //muito feliz
        }
        if(valor == 30) {
          fac3(); //triste
        }
        if(valor == 40) {
          fac4(); //muito triste
        }
        if(valor == 50) {
          fac5(); //língua para fora
        }
        if(valor == 60) {
          fac6(); //morto
        }
        if(valor == 70) {
          fac7(); //assustado
        }
        if(valor == 80) {
          fac8(); //dormindo
        }
        if(valor == 90) {
          fac9(); //confuso
        }
        if(valor == 100) {
          fac10(); //entediado
        }  
        if(valor == 110) {
          fac11(); //apaixonado
        }  
        if(valor == 120) {
          fac12(); //nojo
        }  
        if(valor == 130) {
          fac13(); //raiva
        }
        if(valor == 140) {
          fac14(); //falando
        } 
      }

      if(comando == "old") {
        if(valor == 10) {
          display_olhos(olho_neutro_d, 1);
          olho_direito = 1;
        }
        if(valor == 20) {
          display_olhos(olho_arregalado_d, 1);
          olho_direito = 2;
        }
        if(valor == 30) {
          display_olhos(olho_fechado_cima_d, 1);
          olho_direito = 3;
        }
        if(valor == 40) {
          display_olhos(olho_fechado_baixo_d, 1);
          olho_direito = 4;
        }
        if(valor == 50) {
          display_olhos(olho_morto_d, 1);
          olho_direito = 5;
        }
        if(valor == 60) {
          display_olhos(olho_triste_d, 1);
          olho_direito = 6;
        }
        if(valor == 70) {
          display_olhos(olho_entediado_d, 1);
          olho_direito = 7;
        }
        if(valor == 80) {
          display_olhos(olho_raiva_d, 1);
          olho_direito = 8;
        }
        if(valor == 90) {
          display_olhos(olho_apaixonado_d, 1);
          olho_direito = 9;
        }
      }
      
      if(comando == "ole") {
        if(valor == 10) {
          display_olhos(olho_neutro_e, 2);
          olho_esquerdo = 1;
        }
        if(valor == 20) {
          display_olhos(olho_arregalado_e, 2);
          olho_esquerdo = 2;
        }
        if(valor == 30) {
          display_olhos(olho_fechado_cima_e, 2);
          olho_esquerdo = 3;          
        }
        if(valor == 40) {
          display_olhos(olho_fechado_baixo_e, 2);
          olho_esquerdo = 4;          
        }
        if(valor == 50) {
          display_olhos(olho_morto_e, 2);
          olho_esquerdo = 5;          
        }
        if(valor == 60) {
          display_olhos(olho_triste_e, 2);
          olho_esquerdo = 6;          
        }
        if(valor == 70) {
          display_olhos(olho_entediado_e, 2);
          olho_esquerdo = 7;          
        }
        if(valor == 80) {
          display_olhos(olho_raiva_e, 2);
          olho_esquerdo = 8;          
        }                        
        if(valor == 90) {
          display_olhos(olho_apaixonado_e, 2);
          olho_esquerdo = 9;          
        }
      }
      
      if(comando == "boc") {
        if(valor == 10) {
          display_boca(boca_alegre);
          boca = 1;
        }
        if(valor == 20) {
          display_boca(boca_muito_feliz);
          boca = 2;
        }
        if(valor == 30) {
          display_boca(boca_triste);
          boca = 3;          
        }
        if(valor == 40) {
          display_boca(boca_muito_triste);
          boca = 4;          
        }
        if(valor == 50) {
          display_boca(boca_lingua);
          boca = 5;          
        }
        if(valor == 60) {
          display_boca(boca_aberta);
          boca = 6;          
        }
        if(valor == 70) {
          display_boca(boca_neutra);
          boca = 7;          
        }
        if(valor == 80) {
          display_boca(boca_neutra);
          boca = 8;          
        }
        if(valor == 90) {
          display_boca(boca_nojo);
          boca = 9;          
        }

        
      }
      //***************************************
      //realizar ações: alteração de velocidade
      //***************************************

      if(comando == "vel") {
        vel = valor;
      }


      //**********************************
      //movimentar os motores DC
      //**********************************

      if(comando == "mot") {
        if(valor == 10) {
          mot1(); //movimentar para a frente
        }
        if(valor == 20) {
          mot2(); //movimentar para a direita
        }
        if(valor == 30) {
          mot3(); //movimentar para a esquerda
        }
        if(valor == 40) {
          mot4(); //movimentar para tras
        }
      }

      
    }
  }
}

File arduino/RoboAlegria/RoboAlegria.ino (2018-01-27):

// Robô da Alegria v2.0
//By Igor Fonseca Albuquerque
//   Thiago Ferrauche
//   Yhan Christian
//   Paulo de Azevedo Jr.

//**********************************
//Inicialização de variávies globais
//**********************************

//incluir bibliotecas
#include <SoftwareSerial.h>
#include <Servo.h>
#include "LedControl.h"

#include <Wire.h>
#include <Adafruit_PWMServoDriver.h>

Adafruit_PWMServoDriver pwm = Adafruit_PWMServoDriver();
#define SERVOMIN  150 // this is the 'minimum' pulse length count (out of 4096)
#define SERVOMAX  600 // this is the 'maximum' pulse length count (out of 4096)

LedControl lc = LedControl(9,10,11,4); //Pinos 9 (DIN), 10 (CLK), 11 (CS), 4 displays a serem controlados
SoftwareSerial esp8266(5, 4); //RX pino 5, TX pino 4

//definição dos pinos dos motores
const int motor1Pin1 = 2;
const int motor1Pin2 = 3;
const int motor2Pin1 = 7;
const int motor2Pin2 = 6;
//definião da velocidade dos motores
int motorSpeed = 255; //motor speed (PWM)

//definição de variáveis 
#define DEBUG true //exibir mensagens trocadas entre o ESP8266 e o arduino na porta Serial

int pos1 = 30; //ângulo atual do servo 1
int pos2 = 40; //ângulo atual do servo 2
int pos3 = 135; //ângulo atual do servo 3
int pos4 = 130; //ângulo atual do servo 4
int pos5 = 77; //ângulo atual do servo 5
int pos6 = 40; //ângulo atual do servo 6
int vel = 10; //velocidade dos servos (100 -> 90º em 1 s)(1 -> 90º em 9 s)
int pos1min = 20; //ângulo mínimo do servo 1
int pos2min = 10; //ângulo mínimo do servo 2
int pos3min = 42; //ângulo mínimo do servo 3
int pos4min = 10; //ângulo mínimo do servo 4
int pos5min = 30; //ângulo mínimo do servo 5
int pos6min = 26; //ângulo mínimo do servo 6
int pos1max = 115; //ângulo máximo do servo 1
int pos2max = 170; //ângulo máximo do servo 2
int pos3max = 136; //ângulo máximo do servo 3
int pos4max = 170; //ângulo máximo do servo 4
int pos5max = 150; //ângulo máximo do servo 5
int pos6max = 50; //ângulo máximo do servo 6
int face; //número da face atual
int olho_direito; //número do olho direito atual
int olho_esquerdo; //número do olho esquerdo atual
int boca; //número da boca atual
boolean piscar; //definir se deve ou não piscar os olhos
unsigned long tempo0; //tempo para piscar os olhos

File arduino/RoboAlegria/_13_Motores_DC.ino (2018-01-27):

//***************************************
//Definição dos movimentos dos motores DC
//***************************************

//movimento1 = andar para frente
void mot1()
{
    digitalWrite(motor1Pin1, HIGH);
    digitalWrite(motor1Pin2, LOW);
    digitalWrite(motor2Pin1, LOW);
    digitalWrite(motor2Pin2, HIGH);
    delay(1000);
    digitalWrite(motor1Pin1, LOW);
    digitalWrite(motor1Pin2, LOW);
    digitalWrite(motor2Pin1, LOW);
    digitalWrite(motor2Pin2, LOW);
}

//movimento1 = andar para direita
void mot2()
{
    digitalWrite(motor1Pin1, LOW);
    digitalWrite(motor1Pin2, HIGH);
    digitalWrite(motor2Pin1, LOW);
    digitalWrite(motor2Pin2, HIGH);
    delay(1000);
    digitalWrite(motor1Pin1, LOW);
    digitalWrite(motor1Pin2, LOW);
    digitalWrite(motor2Pin1, LOW);
    digitalWrite(motor2Pin2, LOW);
}

//movimento1 = andar para esquerda
void mot3()
{
    digitalWrite(motor1Pin1, HIGH);
    digitalWrite(motor1Pin2, LOW);
    digitalWrite(motor2Pin1, HIGH);    
    digitalWrite(motor2Pin2, LOW);
    delay(1000);
    digitalWrite(motor1Pin1, LOW);
    digitalWrite(motor1Pin2, LOW);
    digitalWrite(motor2Pin1, LOW);
    digitalWrite(motor2Pin2, LOW);

}

//movimento1 = andar para trás
void mot4()
{
    digitalWrite(motor1Pin1, LOW);
    digitalWrite(motor1Pin2, HIGH);
    digitalWrite(motor2Pin1, HIGH);
    digitalWrite(motor2Pin2, LOW);
    delay(1000);
    digitalWrite(motor1Pin1, LOW);
    digitalWrite(motor1Pin2, LOW);
    digitalWrite(motor2Pin1, LOW);
    digitalWrite(motor2Pin2, LOW);
}

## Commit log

2016-09-20 Documentação
    Documentação completa
    [p1.dxf, p10.dwg, p10.dxf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]
2016-09-20 Atualização da documentação
    Inclusão de pastas com fotos e README
    [robot mk0 - rev1.fzz]
2016-09-26 Atualização do código do Arduino
    Divisão do código do Arduino em partes menores para facilitar a
    manutenção
2016-09-27 Jogo
    Upload do primeiro jogo para o Robô da Alegria
2016-10-09 API para Desenvolvimento
2017-02-18 Updates
    Atualização do shield e partes mecânicas
    [robot mk0 - rev6-1.fzz]
2017-11-20 Update
    Atualização do código da Arduino, da interface (html) e dos esquemáticos
    (Fritzing).
    [robot mk0 - rev7.fzz]
2017-11-20 Update
    Update do código do Arduino
2018-01-27 Updates
    Atualização de circuitos e códigos
    [robot mk0 - rev7.fzz, robot mk0 - rev8.fzz]
